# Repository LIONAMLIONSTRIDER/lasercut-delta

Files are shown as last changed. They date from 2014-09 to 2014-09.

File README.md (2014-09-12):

#lasercut-delta

## Intro

This repo contains a design for 3D a delta-stlye printer, largely built from laser-cut parts. The motivation being a fast-to create printer, accessible to anyone with access to a laser cutter.

Parts are glued together to form final assemblies. If you've ever built an old-school balsa aircraft, you'll be right at home

There is also a [list of other parts](VITAMINS.md) to complete the printer and a [few notes on designing for laser cut parts](LESSONS.md) which I've jotted down.

## Editing

All files are authored using [QCad](http://www.qcad.org/en/) which has proven to work really well for this kind of 2D editing

## Design
The printer is a conventional delta layout. Under active development. Either toothed belt or spectra fishing line can be used

##Arms
Both designs are intended to use magnetic balls glued to the effector and carriages, with bolts in aluminium tubing acting as the arms. 

##HotEnd
The effector is designed to work with the [E3D V6 HotEnd][1], but others can easily be accomodated

##Printing/Cutting
The printer is designed to be cut from 3mm MDF sheet. In all DFX files, later 0 is designed to be cut. All other layers should be hidden/ignored for cutting.

The largest parts currently are the base and top sheets, which have a maximum length of 335mm by 290mm, meaning that it ought to fit onto an A3 laser cutter.

##Status
Currently the body parts and some bearing carriages are cut and assembled. The next step is to finish the bearing carriages and assemble the effector.

[1]: http://e3d-online.com/E3D-v6

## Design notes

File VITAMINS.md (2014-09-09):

#Vitamins

##Hardware
* 18 * 623ZZ Bearings - For linear sliders
* 18 * M3 nut/bolt/washer for securing bearings (8mm thread)
* 12 * [10mm Spherical magnets][3]
* 12 * [M5 Cap-Head bolts for arm-ends][4] 
* 1 * [250mm Diameter Mirror][5] as print surface

##Extrusions
* 3 * [2020 aluminium extrusion][1] - 750mm length
* 12 * [T-Nuts][2] for the extension

[1]: http://www.aluminium-profile.co.uk/acatalog/Aluminium_Profile_with_6mm_Slot.html
[2]: http://www.aluminium-profile.co.uk/acatalog/aluminium_Profile_T_Nuts.html
[3]: http://www.first4magnets.com/sphere-magnets-c45/10mm-dia-n42-neodymium-sphere-magnets-1-4kg-pull-p2452
[4]: http://www.ebay.co.uk/itm/Pack-of-16-M5-X20mm-Steel-Allen-Socket-cap-Head-Bolts-/280630310680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
[5]: http://www.amazon.co.uk/dp/B008GFQ9C4/ref=pe_385721_37038051_TE_3p_dp_1

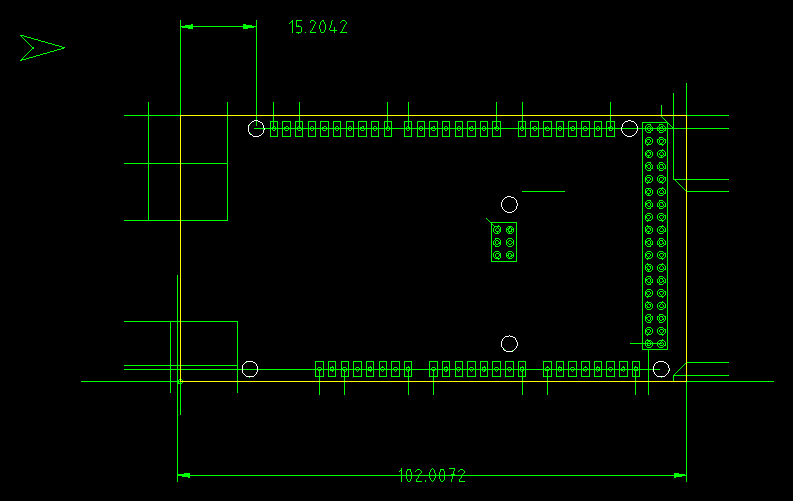
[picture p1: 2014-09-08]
arduino_mega_layout.dxf.png

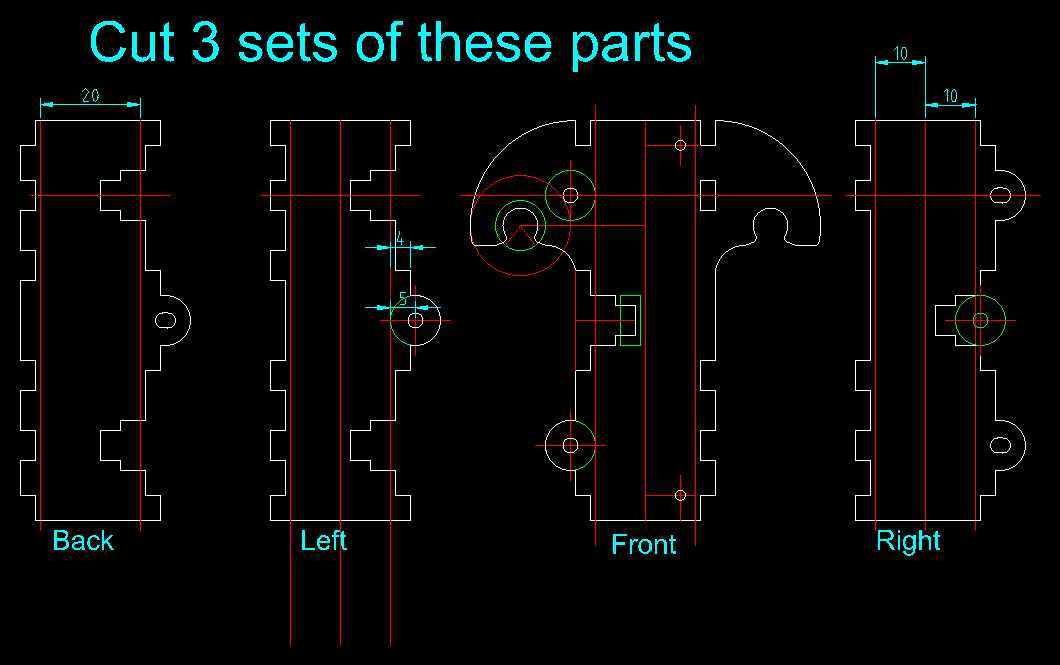
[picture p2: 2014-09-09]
~bearing carriage.dxf.png

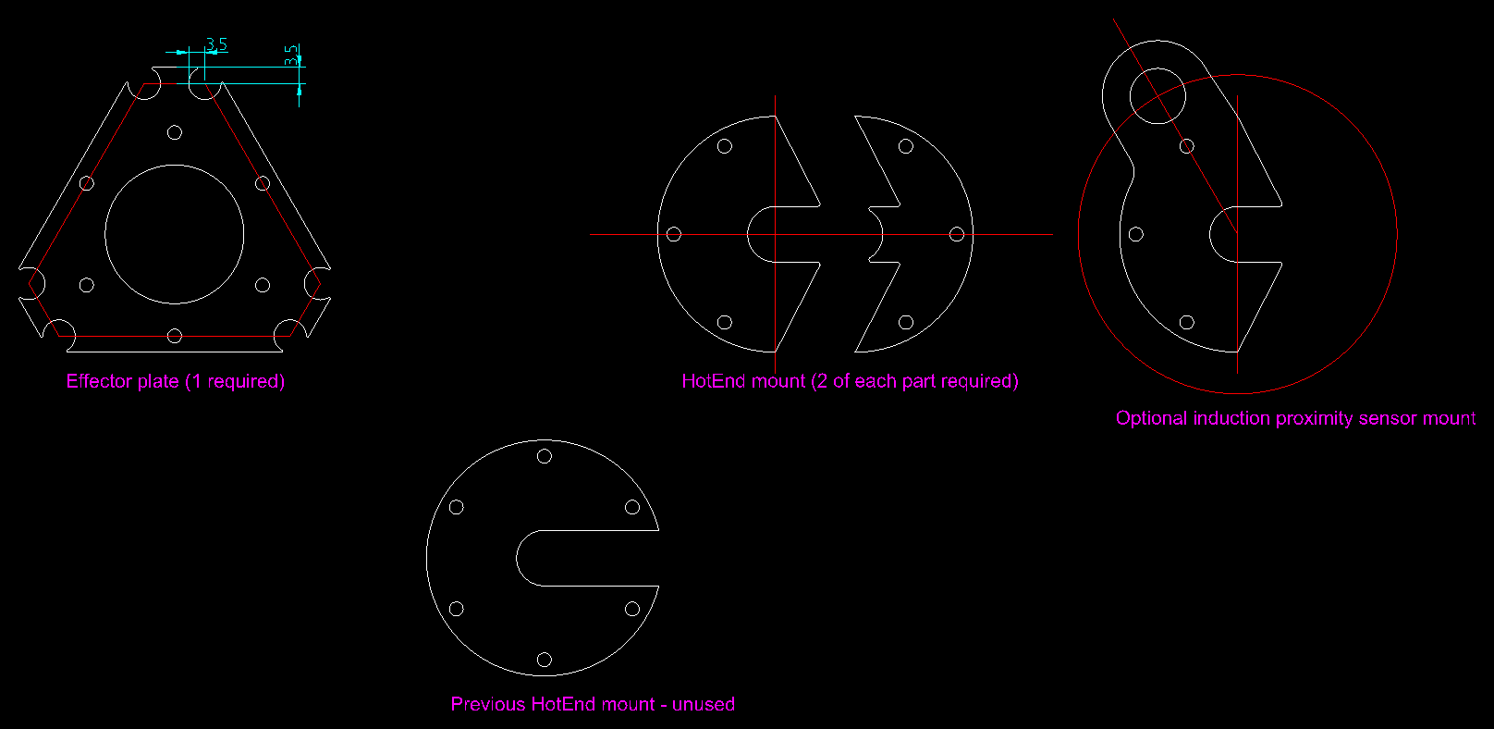
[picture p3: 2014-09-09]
effector.dxf.png

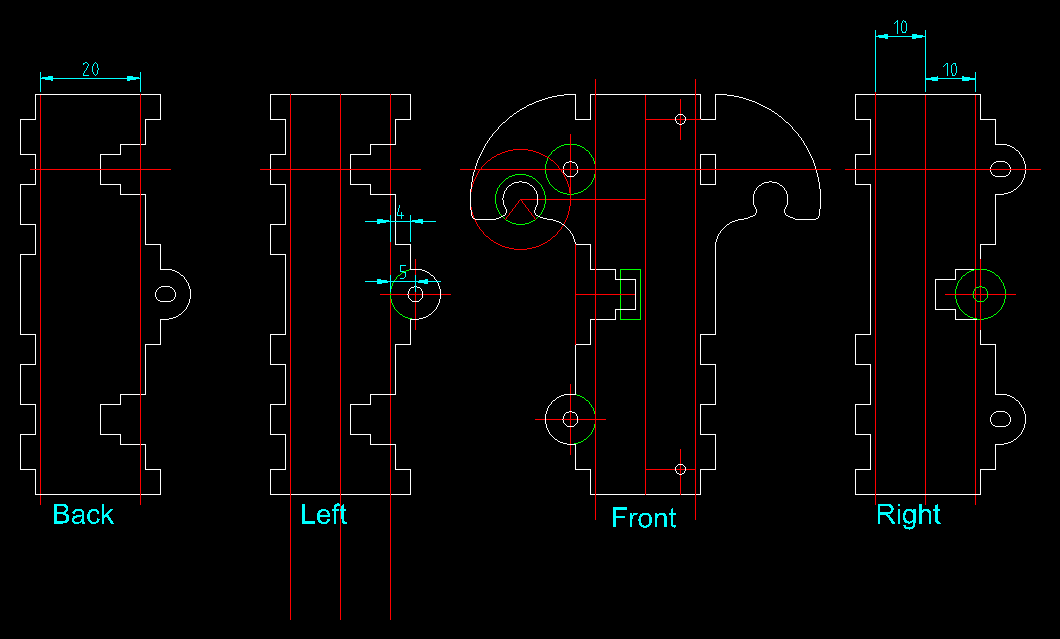
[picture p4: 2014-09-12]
bearing carriage.dxf.png

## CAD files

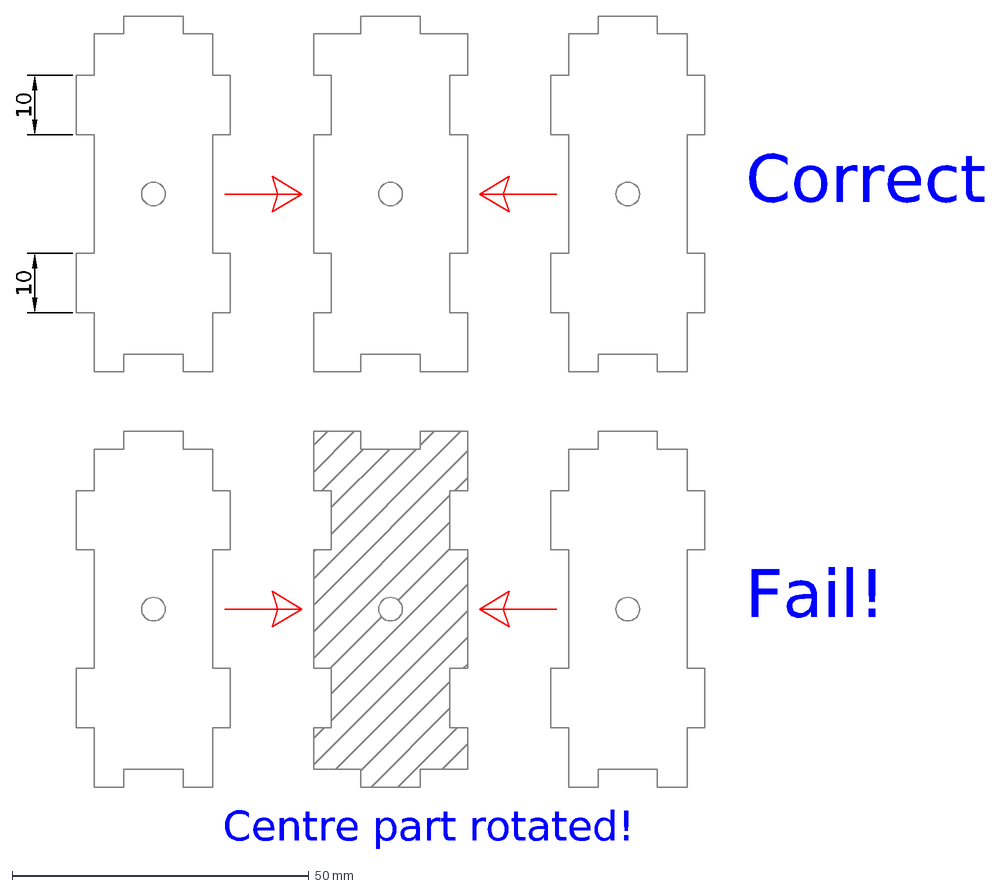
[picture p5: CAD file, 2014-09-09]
docs/assembly-examle.dxf
Correct
Fail!
Centre part rotated!
10

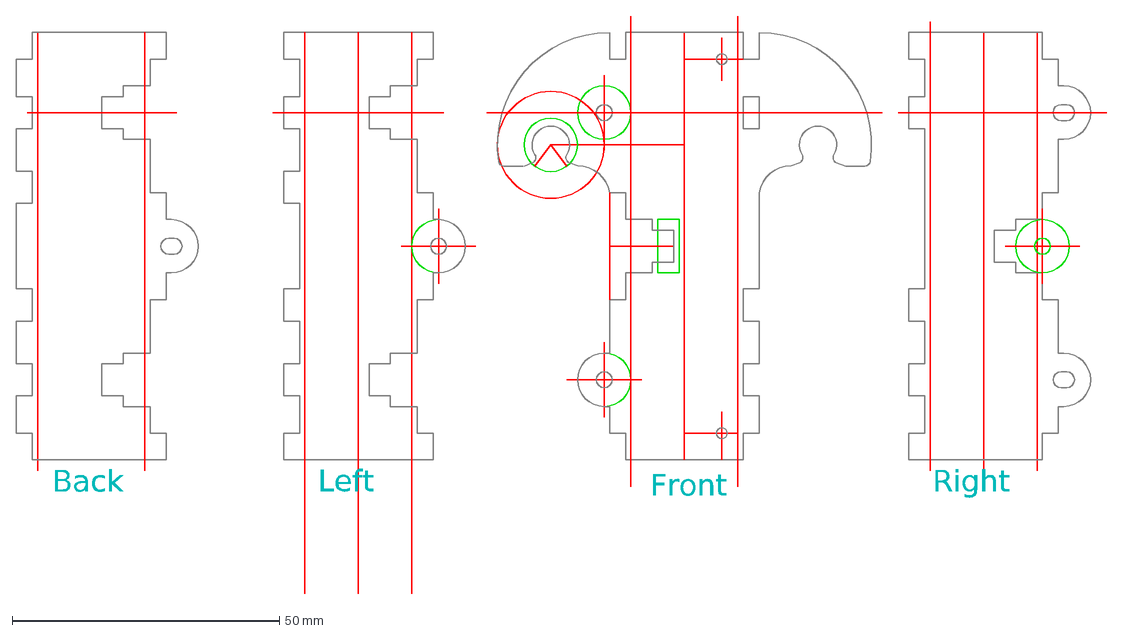
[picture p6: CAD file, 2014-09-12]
bearing carriage.dxf
Front
Left
Back
Right

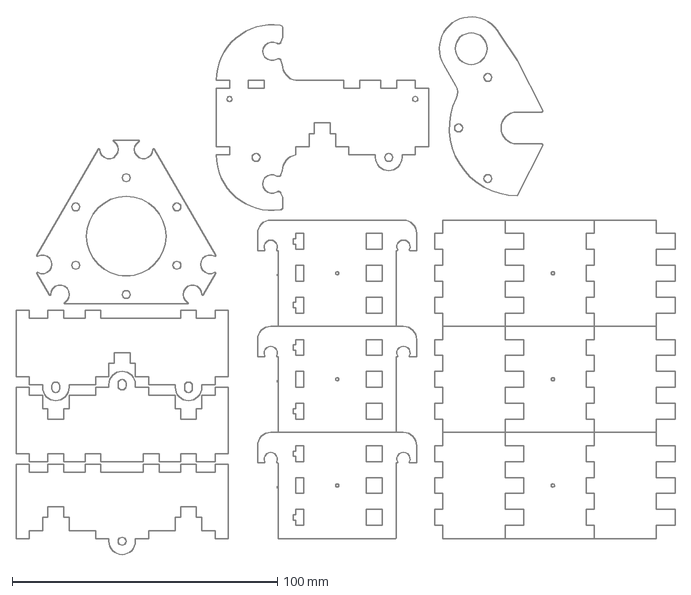
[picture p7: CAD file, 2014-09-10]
print/print6.dxf
248.3 x 202.7 mm

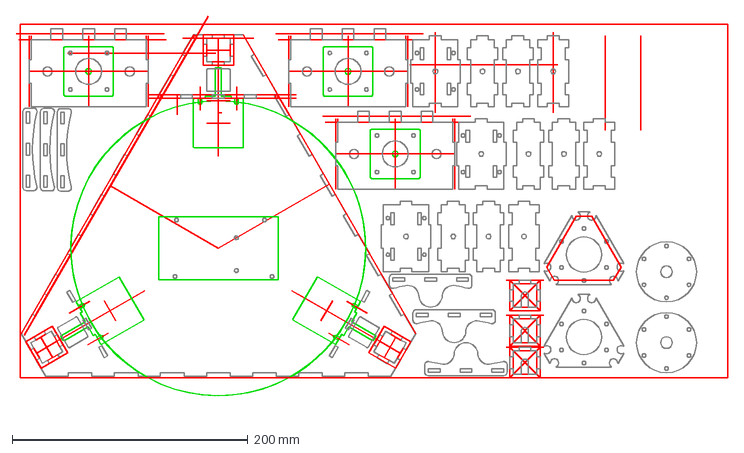
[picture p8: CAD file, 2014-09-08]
print/print1.dxf
603.4 x 336.4 mm

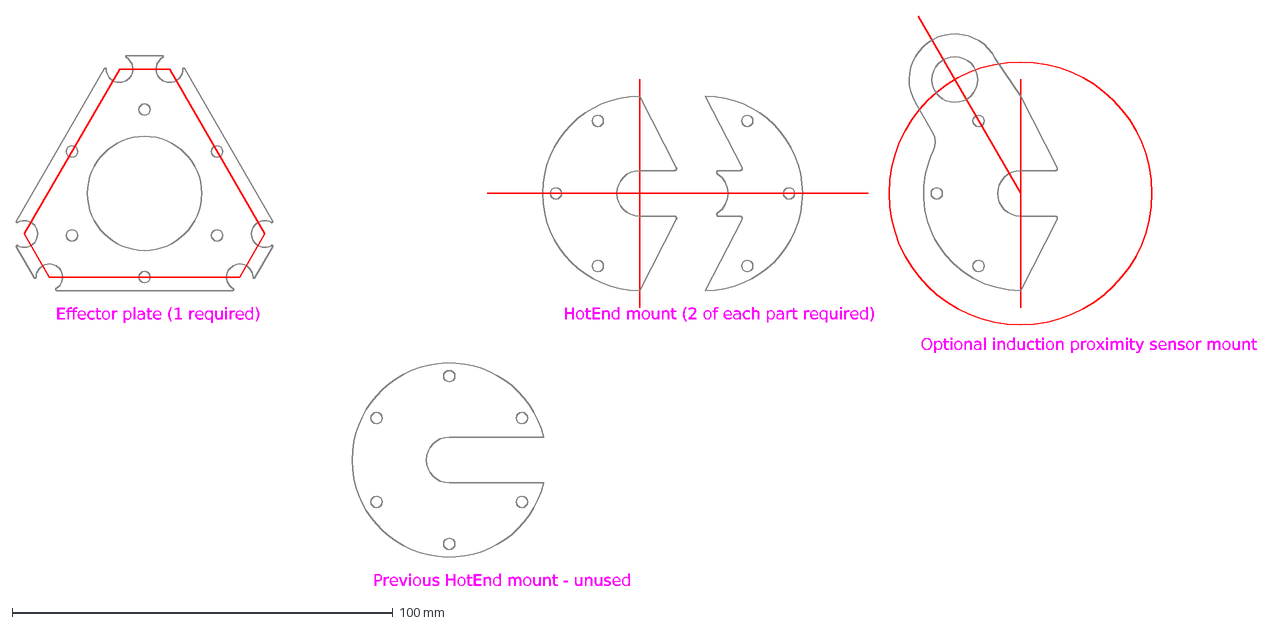
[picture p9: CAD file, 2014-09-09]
effector.dxf
Effector plate (1 required)
HotEnd mount (2 of each part required)
Previous HotEnd mount - unused
Optional induction proximity sensor mount

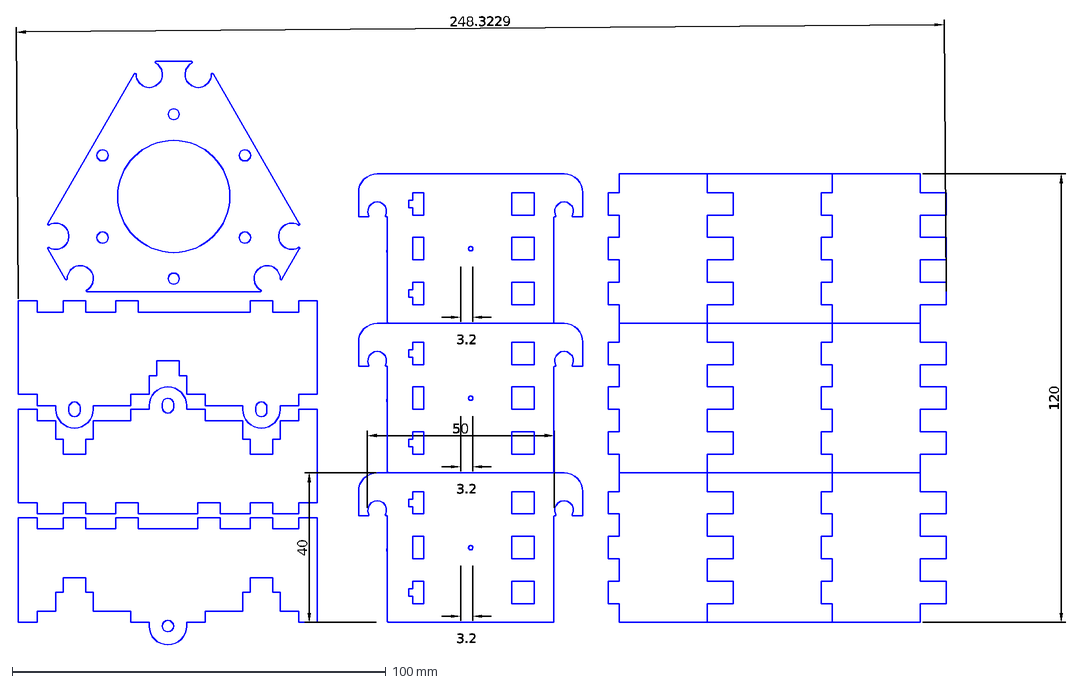
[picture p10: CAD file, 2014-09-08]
print/print6_razorlabs.dxf
50
40
3.2
248.3229
120

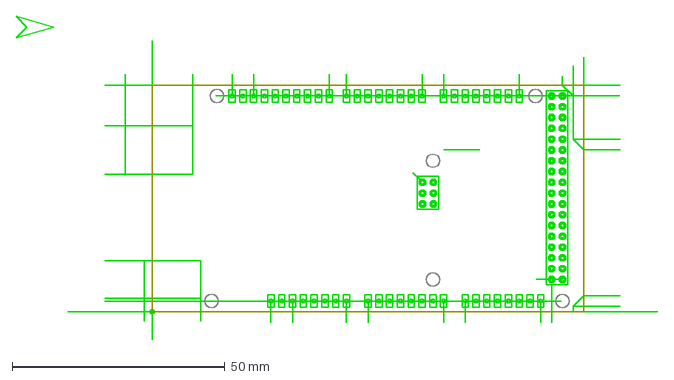
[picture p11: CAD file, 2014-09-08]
arduino_mega_layout.dxf
150.7 x 76.0 mm

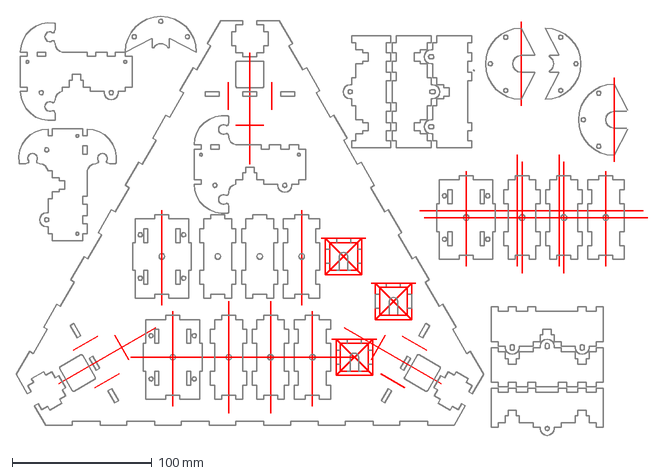
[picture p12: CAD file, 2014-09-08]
print/print3.dxf
452.0 x 299.9 mm

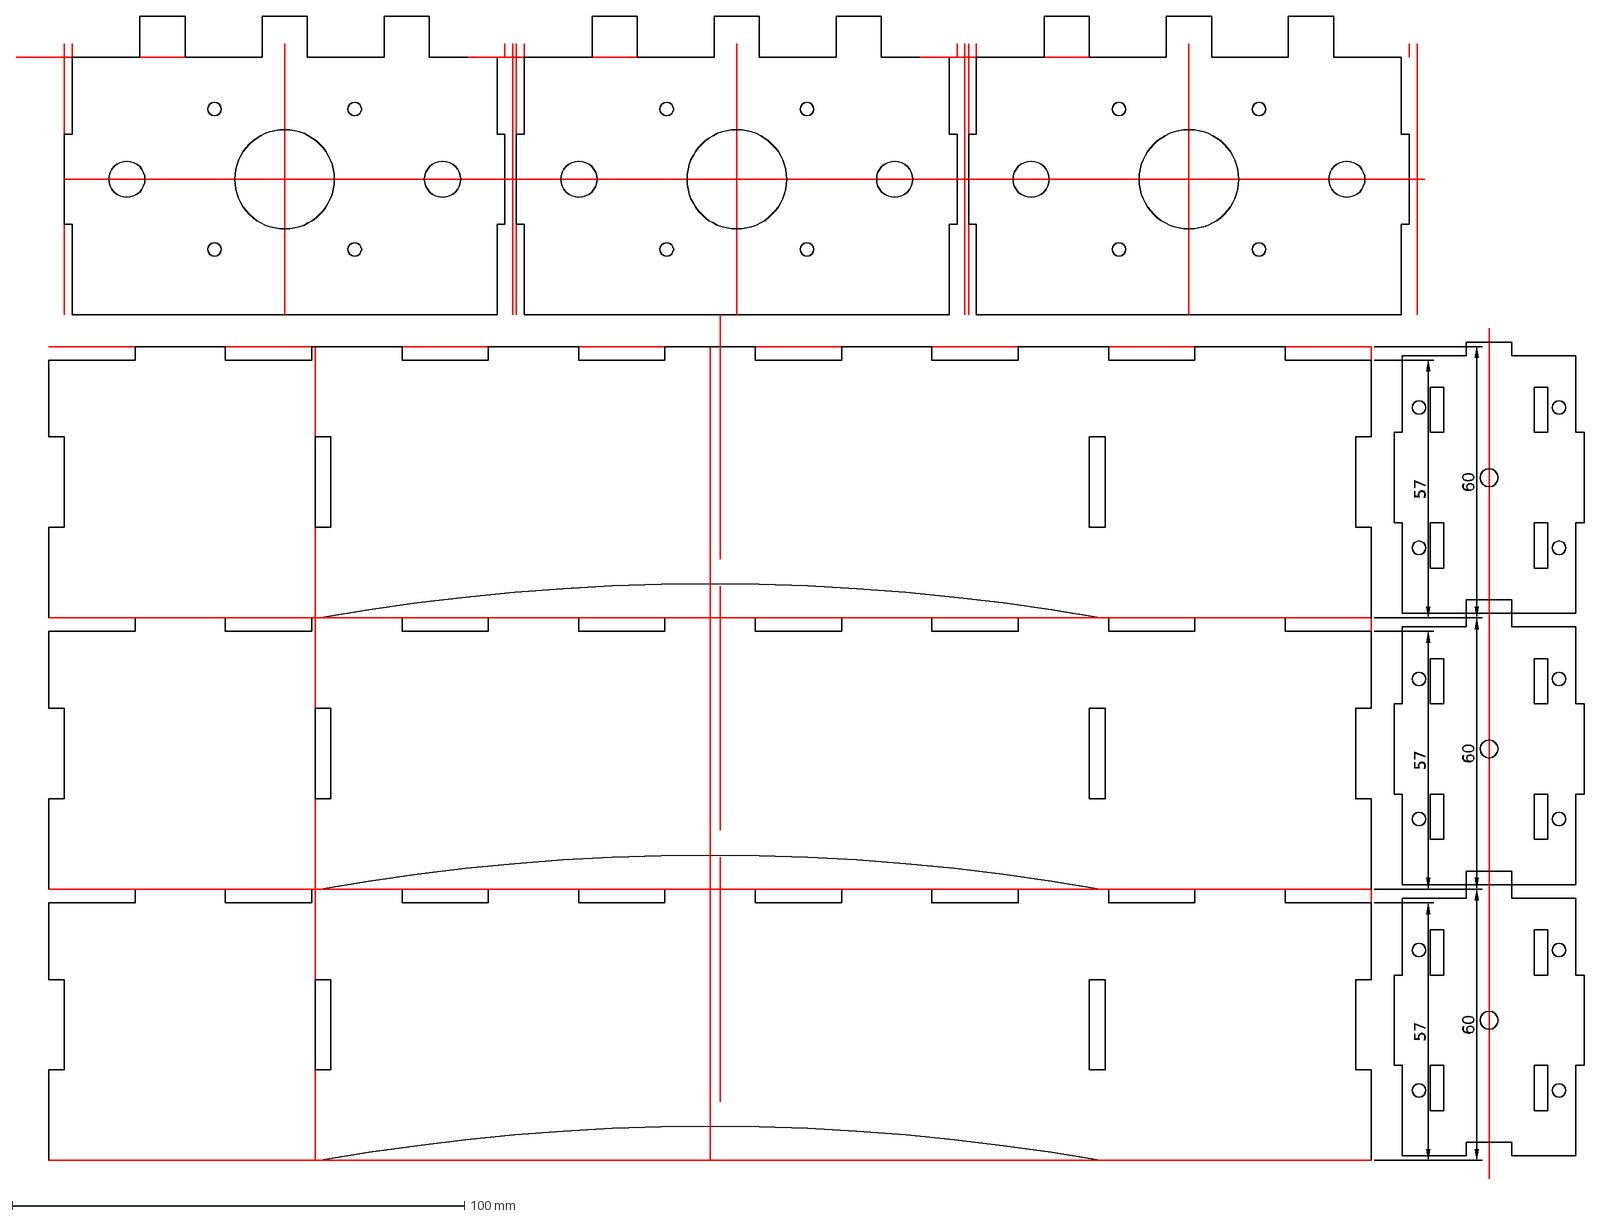
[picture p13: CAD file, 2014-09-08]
print/print4.dxf
60
57

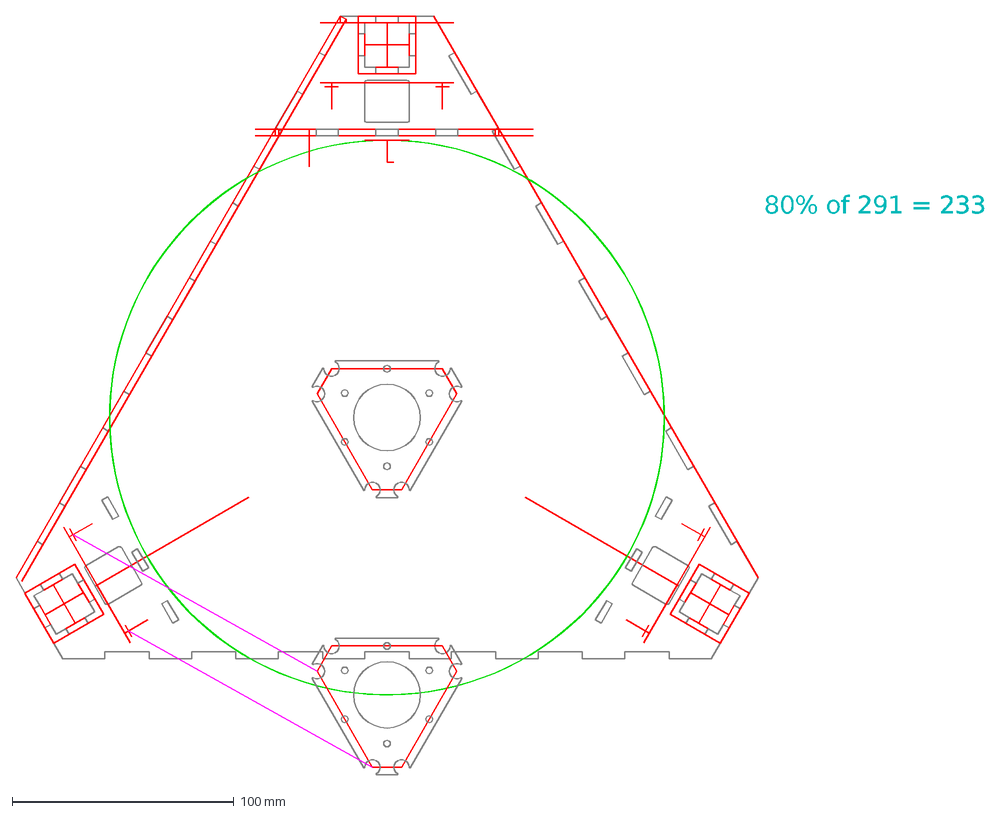
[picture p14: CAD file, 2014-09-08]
Arm Length Calculation.dxf
80% of 291 = 233

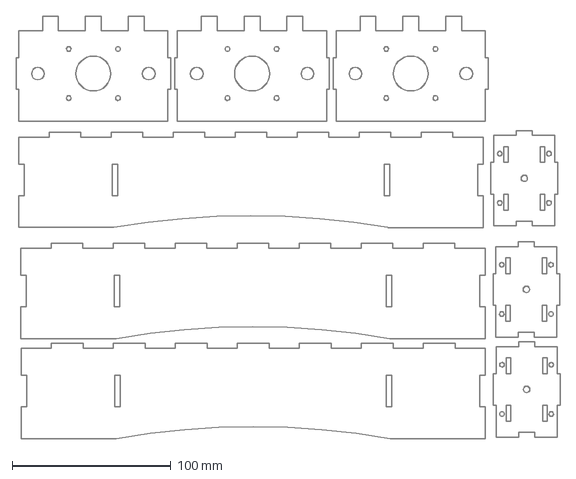
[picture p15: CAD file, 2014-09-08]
print/print5.dxf
342.7 x 266.0 mm

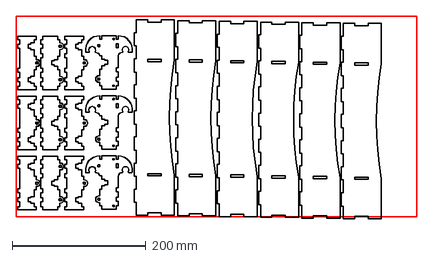
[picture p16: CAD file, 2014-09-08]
print/print2.dxf
600.0 x 303.3 mm

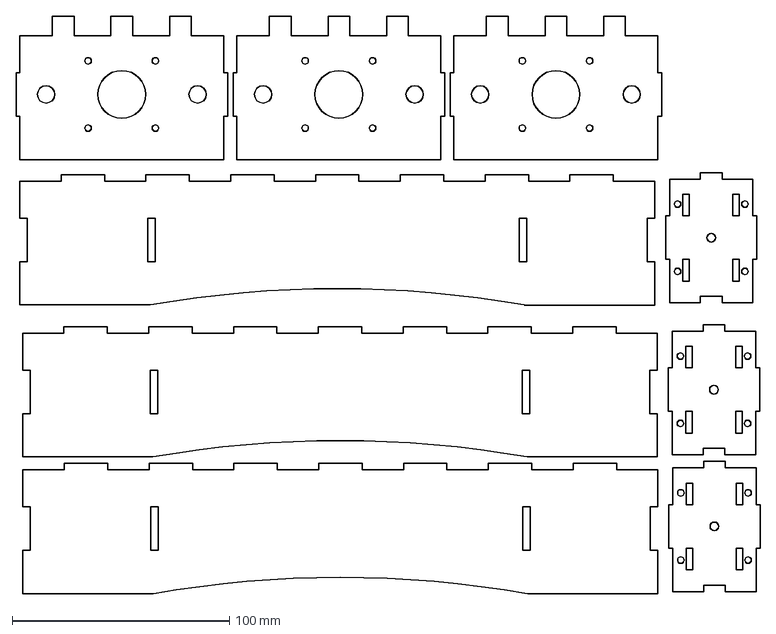
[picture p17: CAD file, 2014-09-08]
print/print5.r15.dxf
342.7 x 266.0 mm

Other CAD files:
base and top.dxf
qcad template.dxf
~bearing carriage.dxf

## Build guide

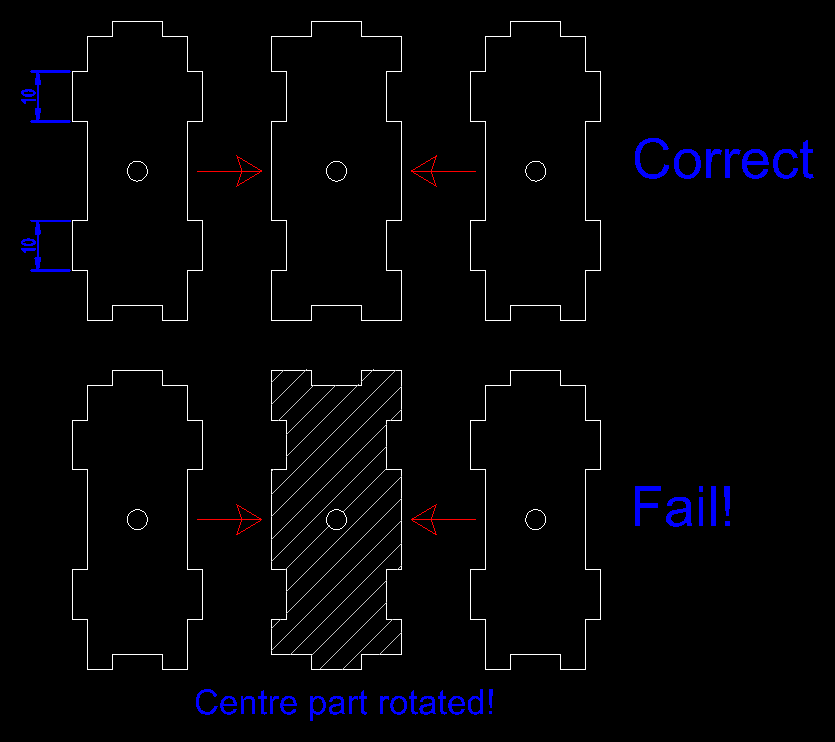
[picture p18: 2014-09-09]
docs/assembly-examle.dxf.png

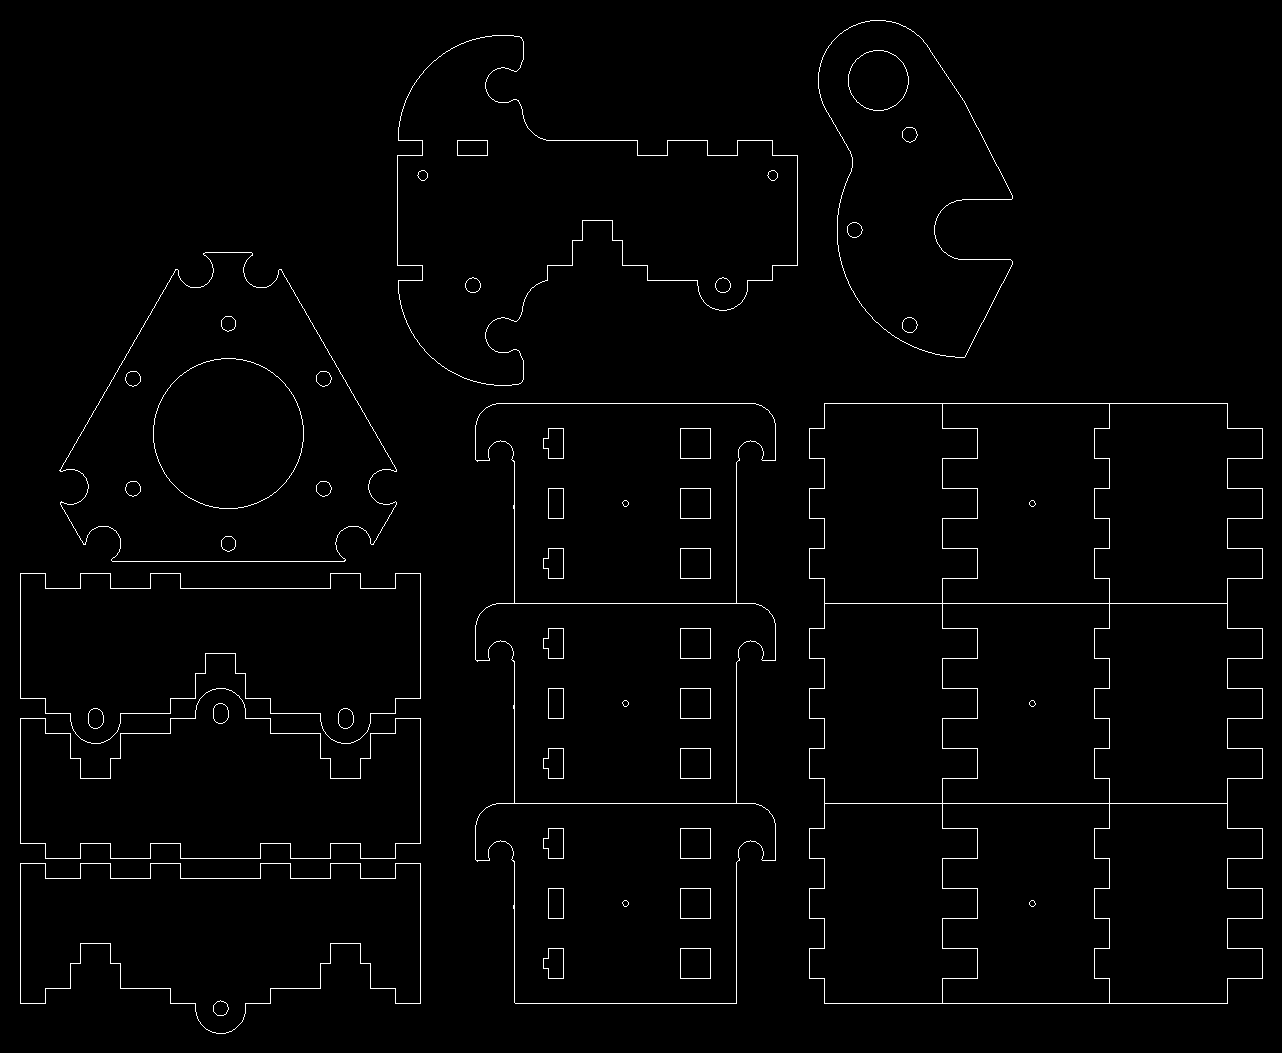
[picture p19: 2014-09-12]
print/print6.dxf.png

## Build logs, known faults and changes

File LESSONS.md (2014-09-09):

#Lessons Learned

A few notes on designing the lasercut delta so far

##Source Control
Use it. I have definitely lost changes through mis-placing copies of files. In the era of GitHub there's no excuse.

DXF Files are hard to diff! The dxf2image.sh script converts all DXF files into PNG images before I check in changes. GitHub (and other tools like [Beyond Compare][1]) supports diffing images, so I can now see differences between revisions

##Do not design parts which can be assembled more than one way
I designed this printer and even I nearly glued parts together incorrectly. An example is the upright supports which glue together to form a square tube. The parts look nicer on screen with their interlocking tabs laid out symmetrically, but this allows you to assemble them with the tabs pointing in the wrong direction:
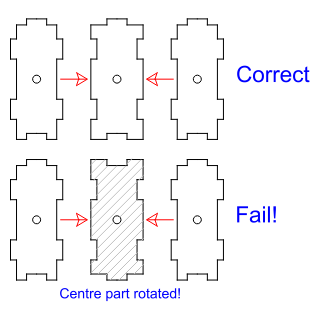
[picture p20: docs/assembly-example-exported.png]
Incorrrect assembly example


There are two solutions I can see to this:

* add an engraving layer to the design, marking part orientation
* change the size of tabs, so that incorrect assembly becomes impossible

Both solutions can be employed at once of course.

##Designing a 3D assembly in 2D is hard
It's incredibly rewarding seeing your parts slot neatly  together and just as frustrating realising that they don't fit.  On several occasions I've designed parts that do not fit correctly or contain design errors. The carriages were originally designed with the bearings in the wrong locations, so the carriages were constrained on 4 points in one axis and only 2 points on the other axis. 

The approach I've found that works is to have a design session, then re-visit the designs a day or two later and think over the changes, trial-fitting the in my mind.

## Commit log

2014-09-08 Initial delivery
    [Arm Length Calculation.dxf, arduino_mega_layout.dxf, base and top.bak000.dxf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]
2014-09-08 Sorted dxf2image.sh and generated initial images
    [base and top.bak000.dxf]
2014-09-09 Added initial list of parts, added cutting notes to bearing carriage
    [~bearing carriage.dxf]
2014-09-09 Corrected upright width
    Corrected upright width
    [base and top.dxf]
2014-09-09 Updated documentation
    added LESSONS.md and linked 250mm mirror in parts list
2014-09-09 Updated lessons learned with example of incorrect assembly
    Updated lessons learned with example of incorrect assembly
    [assembly-examle.dxf]
2014-09-09 Added proximity sensor option
    [effector.dxf]
2014-09-10 Final Print parts for V1
    [print6.dxf]
2014-09-12 labeled parts
    added labels in most DXF files
    [base and top.dxf, bearing carriage.dxf]
